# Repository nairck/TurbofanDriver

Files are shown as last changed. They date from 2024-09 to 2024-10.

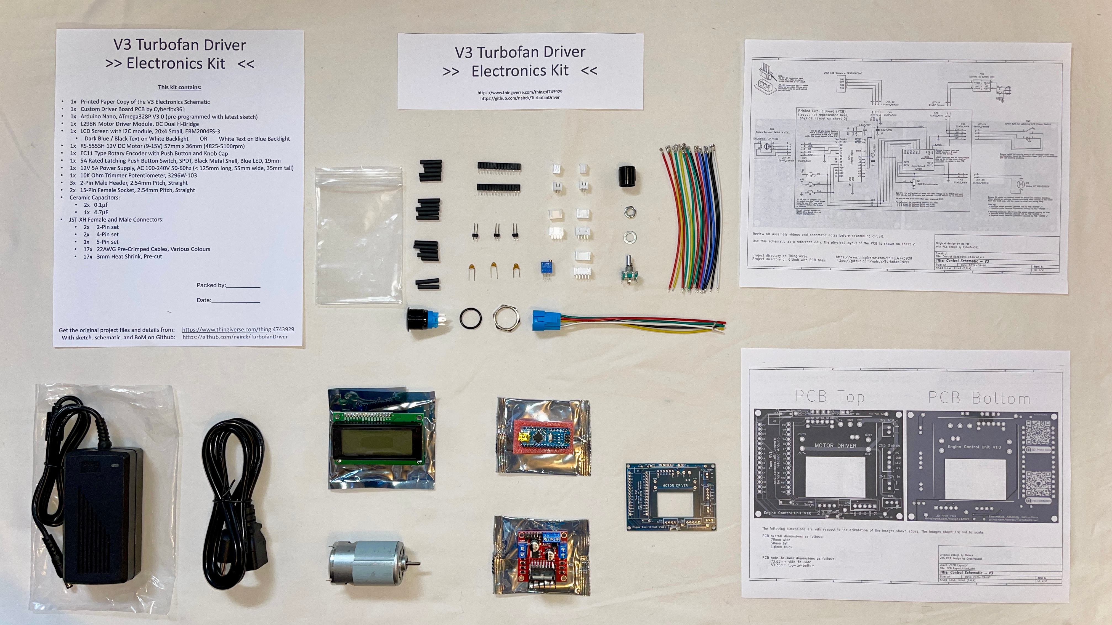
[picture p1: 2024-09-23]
Kit Lists/Electronics_kit.jpeg

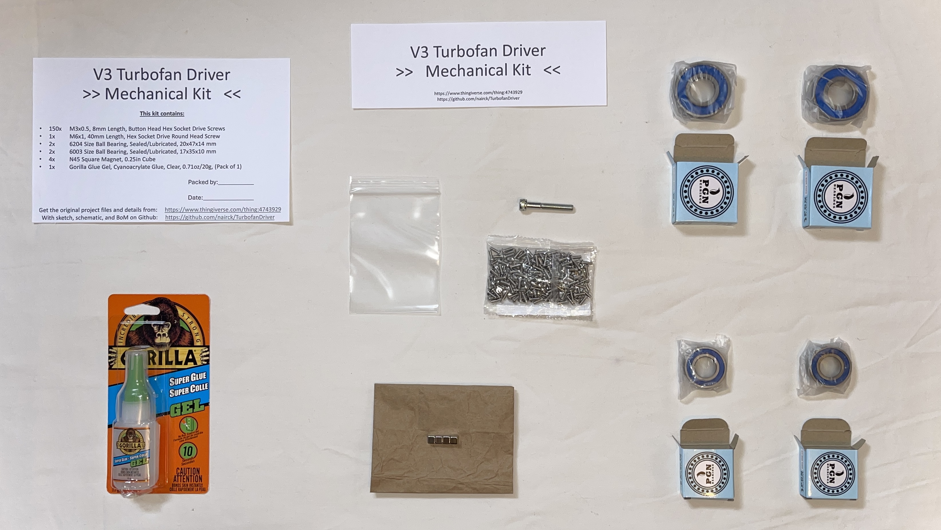
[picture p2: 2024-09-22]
Kit Lists/Mechanical_kit.jpeg

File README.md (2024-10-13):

# TurbofanDriver

Here resides various important files for the 3D Printable Jet Engine - V3 Turbofan Driver:

- Control Sketch   	- C/C++ Arduino code used to program your Arduino Nano using the Arduino IDE.
- Control Schematic     - the electrical schematic for the entire circuit with connection details and notes.
- PCB Gerber ZIP file	- to be uploaded to JLCPCB or PCBWay type online PCB ordering site.
- Bill of Materials	- a detailed list of parts required to build this project, seperated by mechanical, electrical, and 3D printed parts.

Use all V3 files if you are starting this project for the first time.
Use "V2 Archive" as reference only to look back at obsolete schematic and instructions.

See Thingiverse post for main project repository:
- https://www.thingiverse.com/thing:4743929

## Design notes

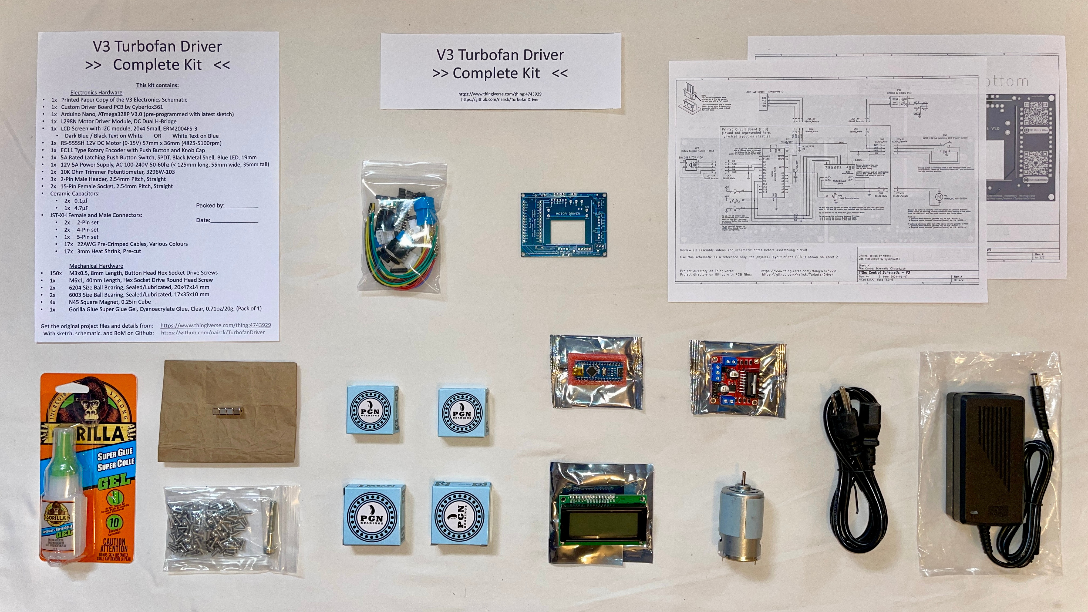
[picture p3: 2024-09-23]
Kit Lists/Complete_kit.jpeg

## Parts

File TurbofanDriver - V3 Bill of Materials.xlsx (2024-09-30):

 | Turbofan Driver - Bill of Materials V3 Upgrade, Aug-Sep 2024 (https://github.com/nairck/TurbofanDriver https://www.thingiverse.com/thing:4743929) Created by Adam B. Johnson
Type | Assy Qty |  |  |  |  | Kit Price (CAD) | Total Price (CAD)
Assembly | 1 | Turbofan Driver, Assembly |  |  |  | $225.00 | $349.19 |  | -
 |  | Turbofan Driver, Electronics and Mechanical Hardware Kit (raw price of single device)
 | 1 | Turbofan Driver, Base/Electronics Assembly |  |  |  | $0.00 | $249.60
 |  | Turbofan Driver, Electronics Assembly Kit (raw price of single device) |  |  |  | $160.00 | $0.00
 | 1 | Turbofan Engine, Mechanical Assembly |  |  |  | $0.00 | $99.59
 |  | Turbofan Driver, Mechanical Assembly Kit (raw price of single device) |  |  |  | $75.00 | $0.00
COTS Electronics |  |  | Vendor | Vendor Part Number | Price per unit (CAD) | Price w/ Tax (CAD) | Total Price (CAD) | link | alternative | alternative
 | 1 | Arduino Nano, ATmega328P V3.0 | Amazon | B0D5LYFRQP | $32.99 | $36.95 | $36.95 | https://www.amazon.ca/ELEGOO-Pre-soldered-ATmega-Compatible-Arduino/dp/B0D5LYFRQP/ | -
 | 1 | L298N Motor Driver Module, DC Dual H-Bridge | Amazon | B0CW243ND1 | $10.75 | $12.04 | $12.04 | https://www.amazon.ca/ShillehTek-Controller-H-Bridge-Raspberry-Mega2560/dp/B0CW243ND1/ | -
 | 1 | EC11 Type Rotary Encoder with Push Button and Knob Cap | Amazon | B07G9Z5CG3 | $11.88 | $13.31 | $13.31 | https://www.amazon.ca/Cylewet-Encoder-Digital-Potentiometer-Arduino/dp/B07G9Z5CG3/ | -
 | 1 | 4A Rated Latching Push Button Switch 1NO1NC SPDT (or 1NO SPST) Black Metal Shell with Blue LED for 19mm 3/4" | Amazon | B0CBRGQGFS | $13.99 | $15.67 | $15.67 | https://www.amazon.ca/gp/product/B0CBRGQGFS/ | -
 | 1 | JST XH Connector Kit 2.54mm 2Pin 3Pin 4Pin 5Pin 6Pin Housing Female and Male Plug, 22AWG Pre-Crimped Cables | Amazon | B0BGBCR9SP | $30.13 | $33.75 | $33.75 | https://www.amazon.ca/Taiss-Connector-Housing-Pre-Crimped-Tweezers/dp/B0BGBCR9SP/ | -
 | 1 | 10K Ohm Trimmer Potentiometer, 3296W-103 | Amazon | B00SWJZMM2 | $11.43 | $12.80 | $12.80 | https://www.amazon.ca/Uxcell-a14052600ux0954-Trimmer-Potentiometer-3296W-103/dp/B00SWJZMM2/ | -
 | 1 | 40 Pin 2.54mm Single Row Female Header & 10 Pieces 40 Pin 2.54mm Single Row Male Header | Amazon | B08CMNRXJ1 | $15.99 | $17.91 | $17.91 | https://www.amazon.ca/Pieces-2-54mm-Single-Female-Header/dp/B08CMNRXJ1/ | -
 | 1 | Heat Shrink Tubing Kit Assorted | Amazon | B09957G2VF | $15.99 | $17.91 | $17.91 | https://www.amazon.ca/Ginsco-730-pcs-Assorted-Sleeving/dp/B09957G2VF/ | -
 | 1 | 12V ≥4A Power Supply, AC Adapter 100-240V 50-60hz (< 125mm long, 55mm wide, 35mm tall) | Amazon | B01GEA8PQA | $17.99 | $20.15 | $20.15 | https://www.amazon.ca/gp/product/B01GEA8PQA/?th=1 | -
 | 1 | Ceramic Capacitor Assortment Kit Capacitors from 0.1uf/100 nF to 10 uF | Amazon | B07P7HRGT9 | $23.99 | $26.87 | $26.87 | https://www.amazon.ca/BOJACK-Ceramic-Capacitor-Assortment-Capacitors/dp/B07P7HRGT9/ | -
 | 1 | RS-555SH 12V DC Motor (9-15V) 57mm x 36mm (4825-5100rpm) | Parts Express | 125-566 | $13.32 | $14.92 | $14.92 | https://www.parts-express.com/Mabuchi-Type-Motor-RS-555SH-12V-DC-Motor-9-15V-57mm-x-36mm-125-566?quantity=1 | - | https://www.opentip.com/Parts-Express-Mabuchi-Type-Motor-RS-555SH-12V-DC-Motor-9-15V-57mm-x-36mm-p-11128796.html | -
 | 1 | LCD Screen with I2C module, 20x4 2004D (rev. C) | Buy Display | ERM2004FS-3 | $19.53 | $21.88 | $21.88 | https://www.buydisplay.com/small-size-blue-lcd-bezel-20x4-arduino-library-character-display-module | https://www.buydisplay.com/small-size-arduino-code-lcd-20x4-i2c-character-display-wide-view-angle | https://www.crystalfontz.com/product/cfah2004dtmiet-character-display-20x4 | -
 | 1 | Driver Board PCB by Cyberfox361 (Upload Gerber files (ZIP file) jlcpcb.com to order) | JLCPCB | - | $4.87 | $5.45 | $5.45 | https://jlcpcb.com/
 |  |  |  |  |  |  |  |  | -
COTS Hardware |  |  |  |  |  |  |  |  | -
 | 1 | M6x1, 40mm Length, Hex Socket Drive Round Head Screw | Amazon | B09TTMDZX2 | $15.99 | $17.91 | $17.91 | https://www.amazon.ca/Cicidorai-Stainless-Machine-Threads-Quantity/dp/B09TTMDZX2?th=1 | -
 | ~137 | M3x0.5, 8mm Length, Button Head Hex Socket Drive Screws (2 Packs of 100) | Amazon | B08H2HTTRT | $12.99 | $14.55 | $29.10 | https://www.amazon.ca/iExcell-Stainless-Socket-Button-Included/dp/B08H2HTTRT/?th=1 | -
 | 1 | 6204 Size Ball Bearing, Sealed/Lubricated, Shielded, or Open, 20x47x14 mm (Pack of 2) | Amazon | B0971X5QJT | $13.35 | $14.95 | $14.95 | https://www.amazon.ca/MAPLE-ACE-6204-2RS-Bearing-20x47x14mm/dp/B0971X5QJT/?th=1 | -
 | 1 | 6003 Size Ball Bearing, Sealed/Lubricated, Shielded, or Open, 17x35x10 mm (Pack of 2) | Amazon | B07GVPRWG6 | $15.08 | $16.89 | $16.89 | https://www.amazon.ca/PGN-6003-2RS-Sealed-Ball-Bearing/dp/B07GVPRWG6/ | -
 | 1 | Gorilla Glue Super Glue Gel, Cyanoacrylate Glue, Clear, 0.71oz/20g, (Pack of 1) | Amazon | B0BZ9YWN35 | $9.99 | $11.19 | $11.19 | https://www.amazon.ca/dp/B0BZ9YWN35/ | -
 |  |  |  |  |  |  |  |  | -
 | 4 | Magnet Square - 0.25" | Sparkfun | COM-08643 | $2.13 | $2.39 | $9.56 | https://www.sparkfun.com/products/8643 | -
 |  |  |  |  |  |  |  |  | -
3D Printed Parts |  | (version 3 items bolded) |  |  |  |  |  |  | -
 | 1 | 30 Tooth Herringbone Gear - V3
 | 1 | Combustion and HPT Casing - V2
 | 1 | Combustion Body - V2
 | 1 | Electronics Bay Cover - V3.1
 | 1 | Fan Casing - V2
 | 1 | Fan Extension - V3
 | 1 | Fan Stator Casing - V3
 | 1 | Fan Tip - V2
 | 1 | Fuel Injectors
 | 1 | Gear Clamp - V3
 | 1 | HPC - V2 - 1
 | 1 | HPC - V2 - 2
 | 1 | HPC - V2 - 3
 | 1 | HPC - V2 - 4
 | 1 | HPC - V2 - 5
 | 1 | HPC - V2 - 6
 | 1 | HPC - V2 - 7
 | 1 | HPC - V2 - 8
 | 1 | HPC - V2 - 9
 | 1 | HPC - V2 - 10
 | 1 | HPC Casing - V2
 | 1 | HPT - V2
 | 1 | Injector Plate
 | 1 | Input Stator - V2
 | 1 of these | Low Pressure Shaft (Front) - V3.1 (M6x1)
 |  | Low Pressure Shaft (Front) - V3.1 (0.25-20)
 |  | Low Pressure Shaft (Front) - V3.1
 | 1 | Low Pressure Spool (Aft) - V3
 | 1 | LPT - V2 - 1
 | 1 | LPT - V2 - 2
 | 1 | LPT - V2 - 3
 | 1 | LPT - V2 - 4
 | 1 | LPT - V2 - 5
 | 1 | LPT - V2 - 6
 | 1 | LPT - V2 - 7
 | 1 | LPT Casing and Motor Mount - V2
 | 1 | LPT Shaft Mount - V2
 | 1 | Magnetic Fan Casing Section - V2
 | 1 | Magnetic Fan Removable Casing Section - V3
 | 1 | Main Fan Blade - V2
 | 1 | Mixer
 | 1 | Motor Clamp - V3
 | 1 | Motor Driver Spacer - V3
 | 1 | Nozzle Adapter - V3
 | 1 | Nozzle-Cone
 | 1 | Power Supply Spacer - V3
 | 1 | Power Supply Spacer, Lateral - V3
 | 1 | Stand and Electronics Bay - V3.1
 | 1 | TN1-006_1_TFD-V3
 | 1 | TN1-006_2_TFD-V3
 | 1 | TN1-006_3_TFD-V3
 | 1 | TN1-118A_TFD-V3
 | 1 | TN1-118B_TFD-V3
 | 1 | TN1-118C_TFD-V3
 | 1 | TN1-118D_TFD-V3
 | 1 | TN1-119A_TFD-V3
 | 1 | TN1-119B_TFD-V3
 | 1 | TN1-119C_TFD-V3
 | 1 | TN1-119D_TFD-V3

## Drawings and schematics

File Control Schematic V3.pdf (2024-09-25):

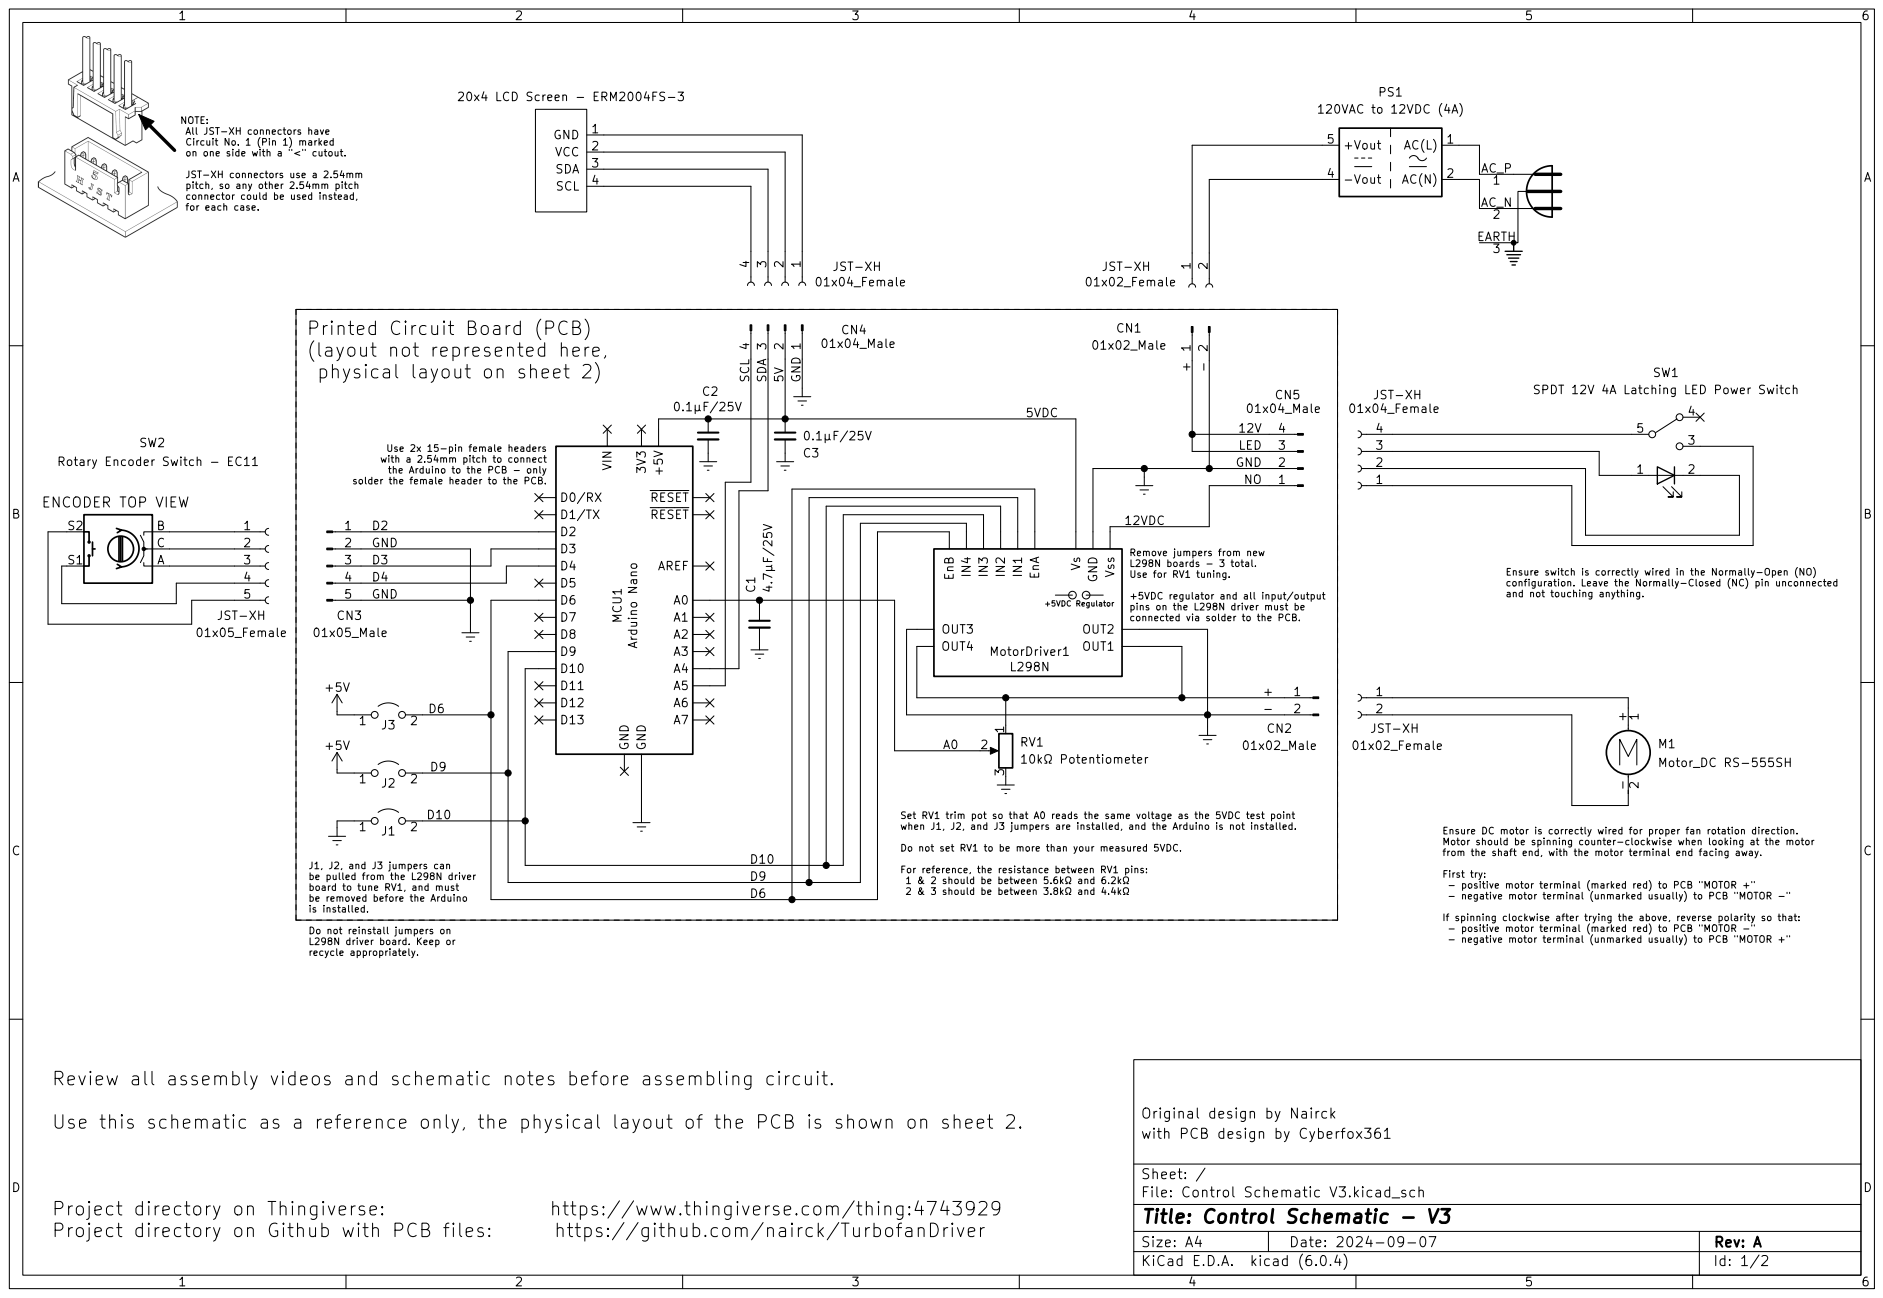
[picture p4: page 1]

physical layout on sheet 2) NOTE:
All JST-XH connectors have
Circuit No. 1 (Pin 1) marked
on one side with a "<" cutout.

JST-XH connectors use a 2.54mm
pitch, so any other 2.54mm pitch
connector could be used instead,
for each case.

and not touching anything. Printed Circuit Board (PCB)
(layout not represented here,

5 SW1 SPDT 12V 4A Latching LED Power Switch

Use 2x 15-pin female headers with a 2.54mm pitch to connect

the Arduino to the PCB - only

connected via solder to the PCB. ENCODER TOP VIEW
GND Review all assembly videos and schematic notes before assembling circuit.

L298N boards - 3 total. Use for RV1 tuning. +5VDC regulator and all input/output pins on the L298N driver must be

Ensure switch is correctly wired in the Normally-Open (NO) configuration. Leave the Normally-Closed (NC) pin unconnected

- negative motor terminal (unmarked usually) to PCB "MOTOR +" Set RV1 trim pot so that A0 reads the same voltage as the 5VDC test point when J1, J2, and J3 jumpers are installed, and the Arduino is not installed. Do not set RV1 to be more than your measured 5VDC. For reference, the resistance between RV1 pins: þÿ 1 & 2 should be between 5.6k© and 6.2k©

Ensure DC motor is correctly wired for proper fan rotation direction. Motor should be spinning counter-clockwise when looking at the motor

J1, J2, and J3 jumpers can be pulled from the L298N driver board to tune RV1, and must be removed before the Arduino

from the shaft end, with the motor terminal end facing away. First try:

- positive motor terminal (marked red) to PCB "MOTOR +"
- negative motor terminal (unmarked usually) to PCB "MOTOR -"

is installed. Do not reinstall jumpers on

If spinning clockwise after trying the above, reverse polarity so that:
- positive motor terminal (marked red) to PCB "MOTOR -"

L298N driver board. Keep or recycle appropriately.

Original design by Nairck
File: Control Schematic V3.kicad_sch Sheet: / with PCB design by Cyberfox361

Use this schematic as a reference only, the physical layout of the PCB is shown on sheet 2.

Id: 1/2 Title: Control Schematic - V3

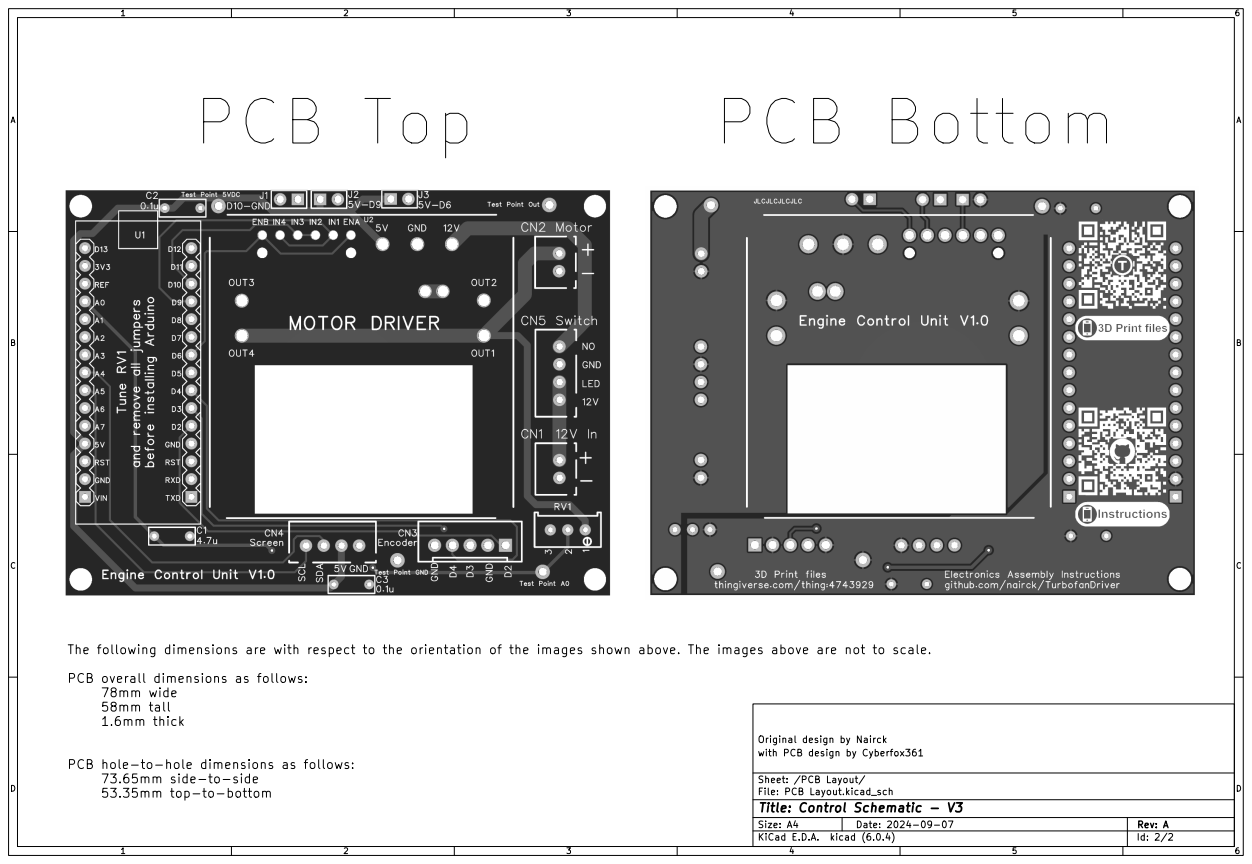
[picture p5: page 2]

The following dimensions are with respect to the orientation of the images shown above. The images above are not to scale.

PCB overall dimensions as follows:
78mm wide
58mm tall
1.6mm thick

Original design by Nairck
with PCB design by Cyberfox361

PCB hole-to-hole dimensions as follows:
73.65mm side-to-side
53.35mm top-to-bottom

Sheet: /PCB Layout/
File: PCB Layout.kicad_sch
Id: 2/2 Title: Control Schematic - V3

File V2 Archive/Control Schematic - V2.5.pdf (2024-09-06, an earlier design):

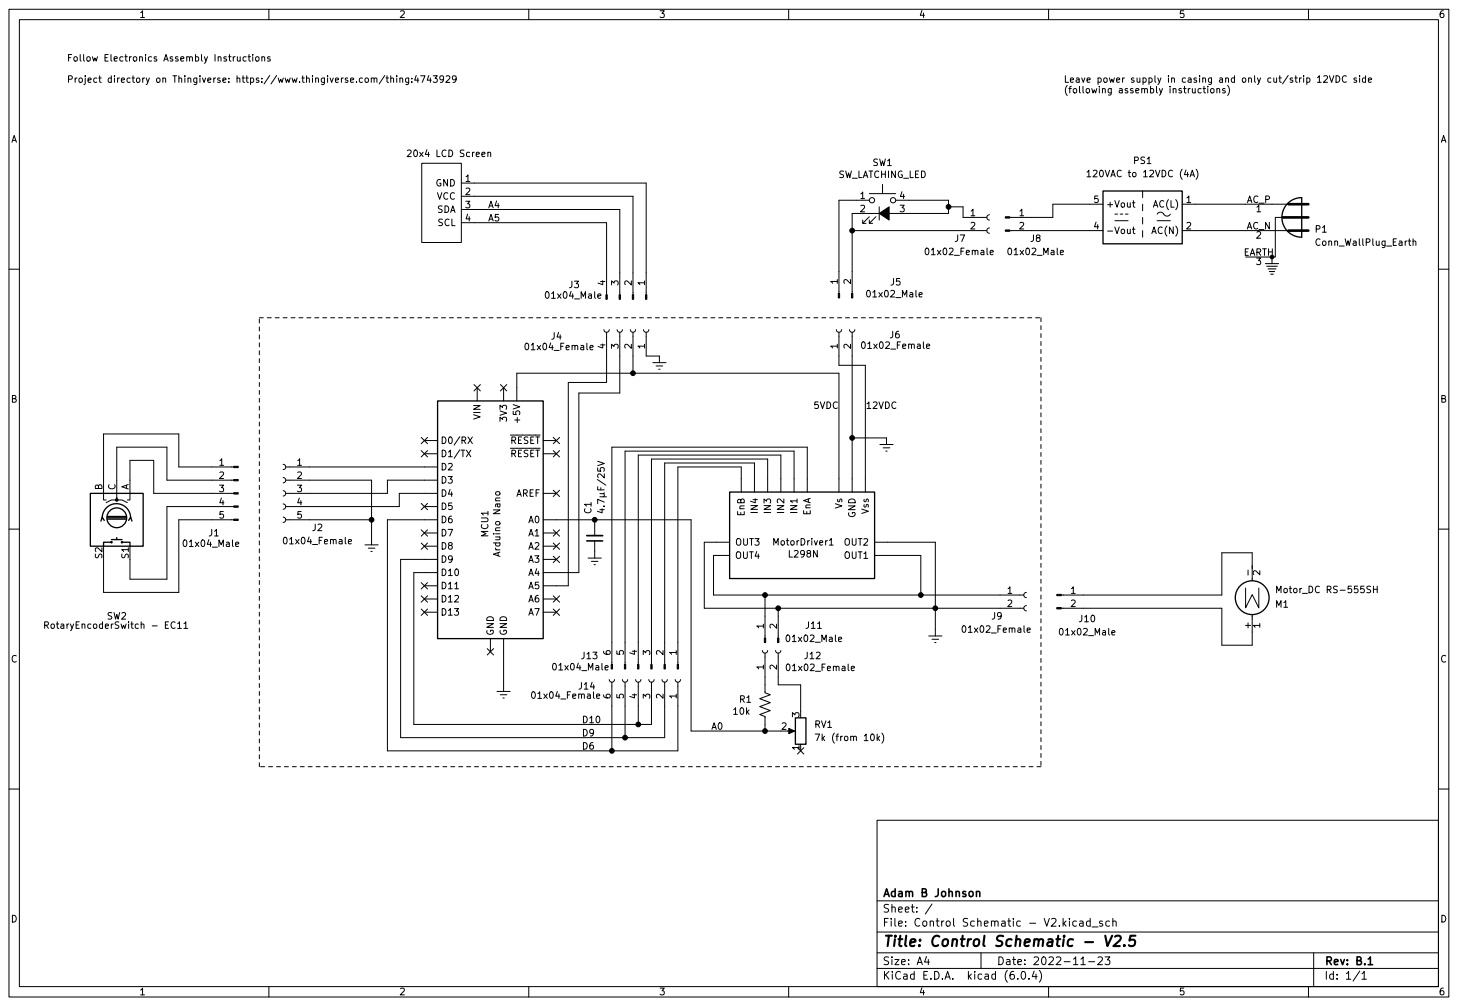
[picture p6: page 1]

A5A4 Follow Electronics Assembly Instructions

File: Control Schematic - V2.kicad_sch Sheet: / Adam B Johnson

Id: 1/1 Title: Control Schematic - V2.5

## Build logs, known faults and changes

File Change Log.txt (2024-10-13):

*** Change Log ***
****************************************************************************************************************

*** updated main Thingiverse (and other sites) post to 'upgrade complete'. Let me know if there any issues, concerns, or suggestions for revisions moving forward! - 13 October 2024 ***

*** Made motor clamp a little wider for less pressure on set. - 23 Sep 2024 ***
 - Motor Clamp - V3.STEP updated
 - Engine Assembly - V3.STEP updated

***Widened Low Pressure Spool (Aft) head size diameter to 11mm for wider bolt heads. Reduced wall thickness on Base face for shorter encoder shafts. - 22 Sep 2024 ***
 - Stand and Electronics Bay - V3.1.STL updated
 - Low Pressure Spool (Aft) - V3.STL updated
 - Engine Assembly - V3.STEP updated

***Updated Arduino control sketch to automatically scan and use the LCD i2c address. No more figuring it out, it's automatic :) - 21 September 2024***

*** Update to control schematic to include 5V regulator and soldering information - 18 Sep 2024 ***

*** Final update to Electronics Bay and Cover to house new PCB and line up with its connector. Update to Motor Clamp to include alignment ridge and make connection better. Improved fitting of various power supplies (within size limits) with addition of spacers. Added small removable spacer for L298N driver during soldering (video to come) - 15 Sep 2024***
 - Electronics Bay Cover - V3.1.STL Added
 - Stand and Electronics Bay - V3.1.STL Added
 - Motor Driver Spacer - V3.STL Added
 - Motor Clamp - V3.STEP updated
 - Engine Assembly - V3.STEP updated

*** Added spacer for side-to-side gap filling of power supplies that are less than 55mm wide. Scale height of spacer as needed to get 55mm 14 Sep 2024***
 - Power Supply Spacer, Lateral - V3.STL updated

*** Added V3 schematic images to this post and uploaded final version to Github. PCB to come soon! - 13 Sep 2024***

*** Added spacer for power supplies that are between 112mm and 125mm. Scale height as needed to get 125mm. 12 Sep 2024***
 - Power Supply Spacer - V3.STL updated

*** Added Complete, Electronics, and Mechanical Kit lists - let me know if there are any issues! - 9 Sep 2024 ***

*** Increased hole size in cowling so key fits more easily. Removed extra holes. 8 Sep 2024***
 - TN1-119A_TFD-V3.STL updated
 - TN1-119B_TFD-V3.STL updated
 - TN1-119C_TFD-V3.STL updated
 - TN1-119D_TFD-V3.STL updated
 - Engine Assembly - V3.STEP updated

*** Included extended tabs in new cowling sections so no M3 nuts needed, only M3 tap, or simply fastener with enough pressure. Adjusted mechanical and combined kit prices - 7 Sep 2024 ***
 - TN1-119B_TFD-V3.STL updated
 - TN1-119C_TFD-V3.STL updated
 - Engine Assembly - V3.STEP updated

*** Increased length of power supply bay in stand and cover to fit anything under 125mm long, 55mm wide, and 35mm tall. - 7 Sep 2024***
 - Electronics Bay Cover - V3.STL added
 - Stand and Electronics Bay - V3.STL updated
 - Engine Assembly - V3.STEP updated

***Uploaded V3 STEP file. No course resolution STL will be uploaded unless requested - 6 Aug 2024***

*** Update to Gear Clamp and Gear - changed M3 with nut to CA glue as shaft key. Improved flexural coupling for installation and push tab for easy removable. - 5 Sep 2024***
 - 30 Tooth Herringbone Gear - V3.STL added
 - Gear Clamp - V3.STL added

*** Updated control sketch to include screen address and turn on backlight by default - 4 Sep 2024 ***

*** Stand and Electronics Bay - V3.STL updated to better fit the LCD screen - 4 Sep 2024 ***
 
*** 3D-printed M6 or 1/4-20 threads made so no larger tap needed. - 28 Aug 2024***
 - Low Pressure Shaft (Front) - V3.1 (M6x1).STL added
 - Low Pressure Shaft (Front) - V3.1 (1/4-20).STL added
 
***Additional pieces to the front added for improved air flow. Adjustment to the base to increase clearance. - more to come - 19 august 2024***

***PCB design in the works! More to come!!! - 19 AUGUST 2024***

***V3 SOFTWARE UPGRADE RELEASED ON GITHUB!  - 11 August 2024***
Updates to voltage measurement filtering, screen updating, and bug fixes for encoder bounce issues and EEPROM speed setpoints.

***V3 SHAFT LINE UPGRADES - 11 August 2024***
 Upgrade requires 40mm M6 or 1/4-20 socket head cap screw and accompanying tap.
 - Low Pressure Shaft (Front) - V3.STL added
 - Low Pressure Spool (Aft) - V3.STL added

****************************************************************************************************************
****************************************************************************************************************
****************************************************************************************************************
****************************************************************************************************************

***V2 MAJOR UPDATE: 23 NOV - 26 DEC 2022 (COMPLETE): ***
***Electrical updates:*** Detailed electronics assembly instructions created; Schematic updated; Code updated; Electronics Bay Assembly video created on YouTube; New files located and kept up to date in GitHub repository; Main Fan Assembly video created on YouTube (link below)

***Mechanical updates:***
Electronics bay and cover to hold regular power supply and fit comfortably the replacement LCD; Entire drive line redesigned with flexural clamping on all rotating blades (except main fan), bores for each connecting shaft to seat concentrically, and added clearance around moving parts; Motor gear and clamp redesigned to be a flexural clamp with snap-in place feature for the gear. Added M3 nut to provide much greater clamping force with the new clamp; Coarse (STL) resolution assembly STL files added to check assembly orientation and configuration - use individual part STL files for higher resolutions print; Master Assembly - V2. STEP file added for further remixing and modifications; Assembly video created on YouTube

 *** ALL UPDATED COMPONENTS ARE MARKED WITH " - V2" ***

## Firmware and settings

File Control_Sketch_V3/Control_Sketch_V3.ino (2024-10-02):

/* Control_Sketch_V3

    This program used an L298N motor driver with a 12VDC motor.
    The 20x4 LCD displays motor speed, turbofan speed, and motor voltage.
    An encoder is used to control the motor speed.
    BUTTON INPUTS TO THE ENCODER:
      Press the button to set speed back to zero.
      Hold the button for 2 seconds to set the Maximum Fan speed.
      Hold the button for 5 seconds to reset the Maximum Fan speed to be uncapped.
    Maximum speed set is remembered inside the program even after power down.

    Visit https://www.thingiverse.com/thing:4743929 for the project directory
    Visit https://github.com/nairck/TurbofanDriver for the Github directory

    Written and designed by Adam B Johnson
    in British Columbia, Canada
    V1 - 15 January 2021
    V2 - 19 November 2022
    V3 - 9 August 2024
       - changed moving average window filter for voltage measurement to single pole RC type low-pass filter (simpler/better).
       - bug fix when turning encoder from higher value to zero wouldn't work. Encoder can bounce still, but zeroing now works a lot better.
       - bug fix where maximum pwm input was equal to maximum allowed minus the deadband
       - bug fixs for EEPROM code, setting new value would reset initialization sometimes or not work at all.
       - Serial monitor will now show encoder position and measured voltage at the sample rate for debugging purposes. Does not affect program when not in use.
       - i2c scanner built into program now, screen address not needed - it will be automatically scanned and used every power up. Included Wire library
       - Updated motor voltage equation to match better

*/

//#######################################  Adjust these values if needed #######################################
//#######################################  Adjust these values if needed #######################################
//#######################################  Adjust these values if needed #######################################
#define chB 2                           //***pin B of the rotary encoder (channel B should be pin 2). Can be non-interrupt capable pin, but will have lower performance
#define chA 3                           //***pin A of the rotary encoder (channel A should be pin 3). Can be non-interrupt capable pin, but will have lower performance
#define pushButton 4                    //***Button pin           
#define motorPWM 6                      //***PWM pin to motor controller 
#define motorDir1 9                     //***motor direction forward pin to driver
#define motorDir2 10                    //***motor direction reverse pin to driver 
#define motorRPMperVolt (5000.0 / 12.0)         //***DC motor max RPM (4825) divided by max voltage (12VDC. Measure both paraments and adjust
//#######################################  End of adjustable parameters #######################################
//#######################################  End of adjustable parameters #######################################
//#######################################  End of adjustable parameters #######################################


// Libraries to include 
#include <Encoder.h>                //Might need to download this library. Tools > Manage Libraries > Search for 'Encoder'
#include <LiquidCrystal_I2C.h>      //Might also need to download this one in the same way.
#include <EEPROM.h>                 //This should have been included when you installed Arduino IDE. No download needed
#include <Wire.h>


// &&&&&&&&&&&&&&&&&&&&&&& &&&&&&&&&&&&&&&&&&&&&&& &&&&&&&&&&&&&&&&&&&&&&&
// &&&&&&&&&&&&&&&&&&&&&&& PROGRAM CONSTANTS &&&&&&&&&&&&&&&&&&&&&&&
// &&&&&&&&&&&&&&&&&&&&&&& &&&&&&&&&&&&&&&&&&&&&&& &&&&&&&&&&&&&&&&&&&&&&&

LiquidCrystal_I2C lcd(0x00, 20, 4);     // Place holder LCD screen object
Encoder myEncoder(chA, chB);            // Encoder object

const float sampleR = 0.5; // 500ms sample rate

int eeAddress = 0;
int eeAddressForInitialization = 100;
byte initializationConst = 0;
byte pwmMax = 255;
int pwmVal = 0;
bool setFlag = false;

const float gearRatio = 2.27;       //fixed gear ratio
int fanSpeed = 0;                   //speed of the turbofan in RPM
int mtrSpeed = 0;                   //speed of the motor in RPM
int deadBand = 30;                  //minimum PWM signal for the motor to move
float vout = 0.0;                   //Voltage out of the motor
float roughMotorVoltage = 0.0;
float oldVolt = 0.0;                //check to see if voltage changes after each loop

long timeNew = 0;                   //time stamp at beginning of loop
long timeOld = 0;                   //time stamp at end of end
long tempTimer = 0;
long oldPos = 0;                    //old position of the encoder
long newPos = 0;                    //new position of the encoder

void setup() {

  Serial.begin(9600);
  pinMode(A0, INPUT);
  pinMode(motorDir1, OUTPUT);
  pinMode(motorDir2, OUTPUT);
  pinMode(motorPWM, OUTPUT);
  pinMode(pushButton, INPUT_PULLUP);
  pinMode(chA, INPUT_PULLUP);
  pinMode(chB, INPUT_PULLUP);

  myEncoder.write(oldPos);
  digitalWrite(motorDir1, HIGH);  //motor direction (FWD = HIGH). DON'T CHANGE. SWITCH THE WIRES IF DIRECTION IS WRONG
  digitalWrite(motorDir2, LOW);   //motor direction (REV = LOW). DON'T CHANGE. SWITCH THE WIRES IF DIRECTION IS WRONG
  analogWrite(motorPWM, 0);

  Serial.println("Scanning for I2C devices...");
  
  Wire.begin();
  byte lcdAddress = scanI2CAddress();

  // If an address is found, initialize the LCD
  if (lcdAddress > 0) {
    Serial.print("LCD found at address 0x");
    if (lcdAddress < 16) Serial.print("0");
    Serial.println(lcdAddress, HEX);

    // Initialize the LCD with the found address
    lcd = LiquidCrystal_I2C(lcdAddress, 20, 4);
    lcd.init();  // Use `init()` instead of `begin()` depending on the library
    lcd.backlight();  // Turn on the backlight
  } else {
    Serial.println("No I2C LCD found.");
  }

  lcd.setCursor ( 1, 0 );
  lcd.print("V3 Turbofan Driver");
  lcd.setCursor ( 0, 2 );
  lcd.print("Adam B. Johnson");
  lcd.setCursor( 0, 3);
  lcd.print("BC, Canada");
  lcd.setCursor ( 16, 3 );
  lcd.print("2024");
  delay(2000);


  //first - flash setup (only works if EEPROM untouched since factory)
  EEPROM.get(eeAddressForInitialization, initializationConst);
  if  (initializationConst != 1) {
    EEPROM.put(eeAddress, 255);
    EEPROM.put(eeAddressForInitialization, 1);
    lcd.clear();
    lcd.setCursor ( 0, 0 );
    lcd.print("First program flash");
    lcd.setCursor( 1, 1);
    lcd.print("detected... ");
    lcd.setCursor ( 2, 2 );
    lcd.print("resetting maximum ");
    lcd.setCursor ( 2, 3 );
    lcd.print("speed setting...");
    delay(10000);
  }

  // get max speed
  EEPROM.get(eeAddress, pwmMax);

  lcd.clear();
  screenSetup();
  zeroNums();
  printSpeeds();
  printVoltage();
  myEncoder.write(0);
  analogWrite(motorPWM, 0);
}


// &&&&&&&&&&&&&&&&&&&&&&& &&&&&&&&&&&&&&&&&&&&&&& &&&&&&&&&&&&&&&&&&&&&&&
// &&&&&&&&&&&&&&&&&&&&&&& MAIN LOOP &&&&&&&&&&&&&&&&&&&&&&&
// &&&&&&&&&&&&&&&&&&&&&&& &&&&&&&&&&&&&&&&&&&&&&& &&&&&&&&&&&&&&&&&&&&&&&

void loop() {

  // start loop timer
  timeNew = millis();

  //get encoder position
  newPos = myEncoder.read();

  // update screen
  if (abs(timeNew - timeOld) >= ((unsigned long)(1000.0 * sampleR))) {
    timeOld = timeNew;

    // read and filter voltage
    float f_cutoff = 0.4;
    float alpha = (2.0 * 3.14 * f_cutoff * sampleR) / ((2.0 * 3.14 * f_cutoff * sampleR) + 1.0);
    roughMotorVoltage = (((1.0 - alpha) * roughMotorVoltage) + (alpha * (analogRead(A0) * 12.15 / 1024.0)));
    roughMotorVoltage = ((int)(roughMotorVoltage * 100.0)) / 100.0;



    if (newPos != oldPos) {
      if ((newPos > 0) && (newPos <= deadBand) && (oldPos < deadBand)) {
        oldPos = newPos;
        newPos = deadBand;
        analogWrite(motorPWM, newPos);
        myEncoder.write(deadBand);
      } else if ((newPos > deadBand) && (newPos <= pwmMax)) {
        analogWrite(motorPWM, newPos);
        oldPos = newPos;
      } else if (newPos > pwmMax) {
        oldPos = pwmMax;
        newPos = pwmMax;
        analogWrite(motorPWM, pwmMax);
        myEncoder.write((int)pwmMax);
        delay(50);
        for (int i = 0; i < 20; i++) {
          lcd.setCursor(i, 0);
          lcd.print(" ");
        }
        lcd.setCursor(1, 0);
        lcd.print("Max Speed Reached!");
        delay(750);
        for (int i = 0; i < 20; i++) {
          lcd.setCursor(i, 0);
          lcd.print(" ");
        }
        lcd.setCursor(2, 0);
        lcd.print("V3 Turbofan Stats");
      } else if ((newPos <= 0) || (newPos < deadBand) && (oldPos >= deadBand)) {
        analogWrite(motorPWM, 0);
        myEncoder.write(0);
        clearNums();
        zeroNums();
        oldPos = 0;
        newPos = 0;
        delay(1000);
      }
    }
    Serial.print("Current encoder position: ");
    Serial.print(newPos);
    Serial.print("      ");
    Serial.print("Measured/filtered motor voltage: ");
    Serial.print(roughMotorVoltage);
    Serial.println(" VDC");

    if (abs(roughMotorVoltage - oldVolt) >= 0.005) {
      // mtrSpeed = motorRPMperVolt * ((2.0 * roughMotorVoltage) - ((float)newPos * 12.0 / 255.0));     // this should be a good enough estimate for armature current, but doesn't work well
      mtrSpeed = motorRPMperVolt * roughMotorVoltage;
      fanSpeed = mtrSpeed / gearRatio;
      oldVolt = roughMotorVoltage;
      clearNums();
      printVoltage();
      printSpeeds();
    }

  }

  // button press protocols
  if (digitalRead(pushButton) == LOW) {
    delay(100);
    if (digitalRead(pushButton) == LOW) {
      delay(300);

      //set current speed to zero - used to turn off fan quickly
      if (digitalRead(pushButton) == HIGH) {
        delay(100);
        if (digitalRead(pushButton) == HIGH) {
          analogWrite(motorPWM, 0);
          for (int i = 0; i < 20; i++) {
            lcd.setCursor(i, 0);
            lcd.print(" ");
          }
          lcd.setCursor(4, 0);
          lcd.print("Speed Reset");
          delay(3000);
          for (int i = 0; i < 20; i++) {
            lcd.setCursor(i, 0);
            lcd.print(" ");
          }
          lcd.setCursor(2, 0);
          lcd.print("V3 Turbofan Stats");
          myEncoder.write(0);
          setFlag = true;
          clearNums();
          zeroNums();
        }
      }

      // Maximum speed set to current value
      if ((digitalRead(pushButton) == LOW)) {
        delay(2000);
        setFlag = false;
        if ((digitalRead(pushButton) == LOW) && (setFlag == false)) {
          byte temp1 = newPos;
          if (temp1 > 255) temp1 = 255;
          if (temp1 < 0) temp1 = 0;
          EEPROM.put(eeAddress, temp1);
          pwmMax = temp1;
          for (int i = 0; i < 20; i++) {
            lcd.setCursor(i, 0);
            lcd.print(" ");
          }
          lcd.setCursor(1, 0);
          lcd.print("Max Speed Set: ");
          lcd.setCursor(16, 0);
          lcd.print(fanSpeed);
          delay(3000);

          //reset maximum speed
          if (digitalRead(pushButton) == LOW) {
            EEPROM.put(eeAddress, 255);
            // get max speed
            pwmMax = 255;
            for (int i = 0; i < 20; i++) {
              lcd.setCursor(i, 0);
              lcd.print(" ");
            }
            lcd.setCursor(2, 0);
            lcd.print("Max Speed Reset");
            delay(3000);
          }
        }
        for (int i = 0; i < 20; i++) {
          lcd.setCursor(i, 0);
          lcd.print(" ");
        }
        lcd.setCursor(2, 0);
        lcd.print("V3 Turbofan Stats");
        setFlag = false;
      }
    }
  }
}


// &&&&&&&&&&&&&&&&&&&&&&& &&&&&&&&&&&&&&&&&&&&&&& &&&&&&&&&&&&&&&&&&&&&&&
// &&&&&&&&&&&&&&&&&&&&&&& FUNCTIONS &&&&&&&&&&&&&&&&&&&&&&&
// &&&&&&&&&&&&&&&&&&&&&&& &&&&&&&&&&&&&&&&&&&&&&& &&&&&&&&&&&&&&&&&&&&&&&

void printVoltage() {
  if ((roughMotorVoltage > 0) && (roughMotorVoltage < 10.0)) {
    lcd.setCursor (12, 3 );
  } else if ((roughMotorVoltage < 15.0) && (roughMotorVoltage >= 10.0)) {
    lcd.setCursor (11, 3 );
  } else {
    lcd.setCursor (12, 3 );
    roughMotorVoltage = 0;
  }
  lcd.print(roughMotorVoltage, 2);
}


void printSpeeds() {
  if (fanSpeed < 100 && fanSpeed >= 10) {
    lcd.setCursor(14, 1);
  } else if (fanSpeed < 1000 && fanSpeed >= 100) {
    lcd.setCursor (13, 1 );
  } else if (fanSpeed < 10000 && fanSpeed >= 1000) {
    lcd.setCursor (12, 1 );
  } else if (fanSpeed == 0) {
    lcd.setCursor (15, 1 );
  } else {
    lcd.setCursor (15, 1 );
    fanSpeed = 0;
  }
  lcd.print(fanSpeed);
  if (mtrSpeed < 100 && mtrSpeed >= 10) {
    lcd.setCursor(14, 2);
  } else if (mtrSpeed < 1000 && mtrSpeed >= 100) {
    lcd.setCursor (13, 2 );
  } else if (mtrSpeed < 10000 && mtrSpeed >= 1000) {
    lcd.setCursor (12, 2 );
  } else if (mtrSpeed == 0) {
    lcd.setCursor (15, 2 );
  } else {
    lcd.setCursor (15, 2 );
    mtrSpeed = 0;
  }
  lcd.print(mtrSpeed);
}


void clearNums() {
  for (int i = 11; i < 17; i++) {
    for (int j = 1; j < 4; j++) {
      lcd.setCursor (i, j);
      lcd.print(" ");
    }
  }
}


void zeroNums() {
  oldPos = 0;
  mtrSpeed = 0;
  fanSpeed = 0;
  roughMotorVoltage = 0.0;
  delay(100);
  printSpeeds();
  printVoltage();
}


void screenSetup() {
  lcd.setCursor (2, 0 );
  lcd.print("V3 Turbofan Stats");
  lcd.setCursor ( 0, 1 );
  lcd.print("Fan Speed:");
  lcd.setCursor (17, 1 );
  lcd.print("RPM");
  lcd.setCursor ( 0, 2 );
  lcd.print("Mtr Speed:");
  lcd.setCursor (17, 2 );
  lcd.print("RPM");
  lcd.setCursor ( 0, 3 );
  lcd.print("Voltage:");
  lcd.setCursor (17, 3 );
  lcd.print("VDC");
}




byte scanI2CAddress() {
  Serial.println("Scanning...");

  for (byte address = 1; address < 127; address++) {
    Wire.beginTransmission(address);
    byte error = Wire.endTransmission();

    if (error == 0) {
      Serial.print("I2C device found at address 0x");
      if (address < 16) Serial.print("0");
      Serial.println(address, HEX);
      return address;  // Return the found address
    } else if (error == 4) {
      Serial.print("Unknown error at address 0x");
      if (address < 16) Serial.print("0");
      Serial.println(address, HEX);
    }
  }

  return 0;  // Return 0 if no I2C device found
}

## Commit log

2022-11-23 V2 Major release from Thingiverse
    Use this new code with the new schematic (V2)
2022-11-23 Addition of "Max Speed Reached!" printout
2022-11-23 Updated page 6 - power supply cabling.
    Added trim instructions to remove strain relief
2022-11-24 Update to pin diagram slide 11
2022-11-25 Update DC motor polarity to match instructions
    Polarity corrected
2022-11-25 Updated DC motor cable instructions
    New DC motor cable is 250mm long; cable is now a twisted pair; colours more obvious.
2022-11-25 Corrected timer rollover
    Not that you should be leaving your circuit on for more than 49 days, but if you do, now that screen will continue to update!
    Line 160:
    old -> if (timeNew - timeOld > 300) {
    new-> if (abs(timeNew - timeOld) > 300) {
2022-12-24 Updates to "THINGS YOU'LL NEED"
    Included mechanical assembly components to purchase and made minor updates to list.
2022-12-24 Add files via upload
    Included CA glue to list of required items for mechanical assembly
2024-06-01 Inlcuded electronics schematic for KiCAD
    [Control Schematic - V2.kicad_sch]
2024-08-11 V3 Upload
    V3 - 9 August 2024
    - changed moving average window filter for voltage measurement to single pole RC type low-pass filter (simpler/better).
    - bug fix when turning encoder from higher value to zero wouldn't work. Encoder can bounce still, but zeroing now works a lot better.
    - bug fix where maximum pwm input was equal to maximum allowed minus the deadband
    - bug fixs for EEPROM code, setting new value would reset initialization sometimes or not work at all.
    - Serial monitor will now show encoder position and measured voltage at the sample rate for debugging purposes. Does not affect program when not in use.
    [Control_Sketch_V3.ino]
2024-08-11 Update Control_Sketch_V3.ino
    Added roughMotorVoltage = 0.0;
    Will push the voltage printed to the screen to 0 when speed reset or zeroed, instead of letting the filter slowly get to 0.
    [Control_Sketch_V3.ino]
2024-08-11 Update Control_Sketch_V3.ino
    Changed sample / refresh rate to 0.5 seconds. better screen visibility
    changed deadband to 25 - adjust as needed.
2024-08-19 Uploaded bill of materials
    [TurbofanDriver - Bill of Materials.xlsx]
2024-08-19 Rename TurbofanDriver - Bill of Materials.xlsx to TurbofanDriver - V3 Bill of Materials.xlsx
    [TurbofanDriver - V3 Bill of Materials.xlsx]
2024-08-28 Uploaded Low_Pressure_Shaft_Front_-_V3.1
    (M6x1) and (0.25-20) options added for 3D printed files
    [TurbofanDriver - V3 Bill of Materials.xlsx]
2024-09-04 update to parts
    updated LCD screen link
    updated fastener length to 40mm and to a socket head cap screw
    [TurbofanDriver - V3 Bill of Materials.xlsx]
2024-09-04 Update
    Update LCD link to blue version and add white alternative link beside it
    Update links to fasteners and fastener description
    [TurbofanDriver - V3 Bill of Materials.xlsx]
2024-09-04 Update Control_Sketch_V3.ino
    Added 0x27 address for new screen
    added lcd.backlight() after initialization to turn on backlight for all screens. Some screens do this by default, but some don't. It doesn't appear to do anything if the backlight is on by default
    [Control_Sketch_V3.ino]
2024-09-04 Update Control_Sketch_V3.ino
    adjusted motor speed equation to correctly estimate speed given drive voltage, measured voltage, and back emf constant
    [Control_Sketch_V3.ino]
2024-09-05 Update to V3 for Gear Clamp and 30-Tooth Gear
    [TurbofanDriver - V3 Bill of Materials.xlsx]
2024-09-06 Add files via upload
    V2 - V3 Upgrade Schematic for folks without the new PCB
2024-09-06 Add files via upload
    For folks upgrading from V2 to V3 who already have the circuit built but want some new code and an updated/accurate schematic. Follow the schematic, not the instructions with respect to motor polarit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
2024-09-06 Add files via upload
    Update to M3 fastener count
    Update to bearing descriptions
    [TurbofanDriver - V3 Bill of Materials.xlsx]
2024-09-07 Update to power supply description and link
    Clarified maximum dimensions and indicated greater than or equal to 4A supply required (can be 5 or 6 amp if available and correct size)
    [TurbofanDriver - V3 Bill of Materials.xlsx]
2024-09-07 Update list of V3 parts
    Included V3 electronics bay cover to V3 list.
    [TurbofanDriver - V3 Bill of Materials.xlsx]
2024-09-07 Updated to power supply description and link
    [TurbofanDriver - V3 Bill of Materials.xlsx]
2024-09-07 Update to bearings, and kit cost
    Updated bearings to sealed/lubricated type and updated mechanical kit cost
    [TurbofanDriver - V3 Bill of Materials.xlsx]
2024-09-08 Update SW1 connector silkscreen to CN5
    Also added line labels to ensure connector pins are matched to PCB pins visually and clearly.
2024-09-08 Included PCB dimensions on sheet 2
2024-09-09 PCB image updated
    PCB image updated - jumper on L298N to drive 5V regulator and power 5V logic circuit added on custom PCB so that L928N jumper can be use to tune RV1 and left off after.
2024-09-13 Final update to PCB images
2024-09-15 Updates
    Update to magnet cost (mistake not converting to CAD from USD)
    Updated 3D printed list, updates to Electronics Base, Cover, and Motor Clamp. Addition of Motor and PCB Spacers
    [TurbofanDriver - V3 Bill of Materials.xlsx]
2024-09-18 Update to L298N driver notes
    update to include 5V regulator on information and note about soldering all the L298N pins to PCB.
2024-09-18 Correct 5V regulator jumper symbol
2024-09-22 Included automatic LCD screen address scan
    Included automatic LCD screen address scan, adjusted filter value off a bit so response on screen appears quicker
2024-09-25 Updated PCB image with final updates
2024-09-25 Updated motor voltage equation
2024-09-30 Alphebetized printed parts order and cleaned up
    [TurbofanDriver - V3 Bill of Materials.xlsx]
2024-09-30 Small update to formatting
    [TurbofanDriver - V3 Bill of Materials.xlsx]
2024-10-02 Updated serial printing text for easier debugging
